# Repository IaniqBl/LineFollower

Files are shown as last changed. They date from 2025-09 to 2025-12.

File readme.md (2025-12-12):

# LineFollower

Mijn LineFollower  
afbeelding

## specifications

microcontroller: Arduino Nano

motors: N20 1/50 500RPM

h-bridge: DRV8833

sensors: QTR-8A

batteries: 2S LiPo 1500mAh

wireless communication: HC08

distance sensor - motors: 10,5cm

weight: x

speed: x

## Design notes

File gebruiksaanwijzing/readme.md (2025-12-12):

# Gebruiksaanwijzing

### opladen / vervangen batterijen
Koppel de batterij los van de linefollower.  
Gebruik een balanceerlader om hem via de balansconnector op te laden.  
Koppel los na het opladen en laat de batterij rusten.  
Koppel de batterij terug aan de linefollower.  

### draadloze communicatie
#### verbinding maken
Gebruik de Serial Bluetooth Terminal app.  
Ga naar devices=>Bluetooth BLE=>Scan selecteer het juiste device.  
Keer terug en klik naast het vuilbakje op connect.  

#### commando's
debug [on/off]  : Toon 1 maal de debug waardes  
start : Start de linefollower
stop : Stopt de linefollower  
set cycle [µs] : Stelt de cyclus tijd in
set power [0..255] : Stelt de power in (255 => 8.4V)
set diff [0..1] : Stelt de diff in  
set kp [0..] : Stelt de kp in  
set ki [0..] : Stelt de ki in  
set kd [0..] : Stelt de kd in  
calibrate black : Calibreer de zwarte waardes  
calibrate white : Calibreer de witte waardes  

### kalibratie
Zet de linefollower op de zwarte lijn en gebruik het calibrate black command. Deze maakt meerdere metingen en pakt het gemiddelde hiervan.  
Zet de linefollower op de witte achtergrond en gebruik het calibrate white command.  

### settings
De robot rijdt stabiel met volgende parameters: 
Kp : 9.00  
Ki : 0.00  
Kd : 0.14  
Diff : 0.55  
Power : 120  

### start/stop button
uitleg locatie + werking start/stop button
Knop bevindt zich op de pcb. Dit is een toggle interrupt laag actieve knop.  
Deze zet een flag aan, die in de loop dezelfde variabele run toggelt.

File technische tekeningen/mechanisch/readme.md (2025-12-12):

## Motor Mounts

Dit project verwijst naar [deze motor mount](https://www.printables.com/model/784474-n20-motor-mount), een origineel ontwerp van de auteur.  
Gelicenseerd onder [Creative Commons BY-NC-SA 4.0](https://creativecommons.org/licenses/by-nc-sa/4.0/)

🔒 **Licentievoorwaarden:**
- ✅ Gebruik en aanpassing toegestaan
- ❌ Geen commercieel gebruik
- ✅ Delen toegestaan onder dezelfde licentie
- ❌ Niet delen zonder naamsvermelding

> “Deze motor mount is gemarkeerd als originele creatie door de auteur. Gebruik vereist correcte attributie en mag niet commercieel zijn.”

---

## N20 Dust Cover

Dit project verwijst naar [deze N20 dust cover](https://www.myminifactory.com/object/3d-print-n20-motor-dust-cover-101243), ontworpen om de motor te beschermen tegen stof.  
Model door de originele auteur, gelicenseerd onder [Creative Commons BY-NC-SA 4.0](https://creativecommons.org/licenses/by-nc-sa/4.0/)

🔒 **Licentievoorwaarden:**
- ✅ Gebruik en aanpassing toegestaan
- ❌ Geen commercieel gebruik
- ✅ Delen toegestaan onder dezelfde licentie
- ❌ Niet delen zonder naamsvermelding

> “Deze dust cover is gemarkeerd als originele creatie door de auteur. Gebruik vereist correcte attributie en mag niet commercieel zijn.”

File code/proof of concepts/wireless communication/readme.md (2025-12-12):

# draadloze communicatie proof of concept
minimale hard- en software waarmee aangetoond wordt dat duplex kan gecommuniceerd worden tussen de microcontroller en een [laptop|smartphone], gebruik makend van [Arduino IDE en Serial Bluetooth Terminal]
<br />
### configuratie
Baudrate Bluetooth 19200  
RX pin van HC08 op D8  
TX pin van HC08 op D7  

Baudrate Seriele 115200  

### opmerkingen

### gebruiksaanwijzing
Stuur test via de app of seriele monitor. Deze stuurt TEST terug naar seriele monitor of app, afhankelijk waar je deze command hebt gestuurd.  
De ingebouwde Led word getoggled door test te sturen.

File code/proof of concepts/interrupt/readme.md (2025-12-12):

# start/stop interrupt proof of concept
Stap 1: Maak de schakeling na volgens het schema.  
Stap 2: Verbind Arduino met PC en upload de code.  

Knop indrukken is ingebouwde Led aan, nog eens drukken is uit.
Media (3)

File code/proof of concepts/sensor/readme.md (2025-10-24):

# Sensoren proof of concept

Stap 1: Maak de schakeling na volgens het schema.  
Stap 2: Verbind de USB met de PC en selecteer de juiste COM poort.  
Stap 3: Open de seriële monitor en beweeg de sensor over de test lijn.  
Voor betrouwbare waarden moet je deze sensor op dezelfde hoogte verschuiven.  
Sensor over zwart => hoge waarde  
Sensor over wit => lage waarde   
afbeelding

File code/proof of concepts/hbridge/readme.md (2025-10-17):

# H-Bridge proof of concept

Stap 1: Maak de schakeling na volgens het schema.  
Stap 2: Verbind Arduino met PC en upload de code.  
Stap 3: Batterijen insteken. En de beide motors zouden moeten draaien.  

Hieronder zie je een foto van mijn schakeling, ik heb momenteel de batterij vervangen door een voeding + Buck step-down convertor omdat ik wacht op mijn batterij.



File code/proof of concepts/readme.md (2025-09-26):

# Proof of Concepts

Een proof of concept is een combinatie van minimale hard- en software om eenvoudig aan te tonen dat iets werkt.  
Proof of concepts kunnen enerzijds als eerste poging dienen om een bepaald onderdeel van het project werkend te krijgen. Anderzijds kunnen ze tijdens het debuggen van het finale project dienen als test om eventuele hardware problemen te elimineren bij onduidelijke problemen.
<br />  
<br />
Een proof of concept bestaat uit
* een elektronisch schema (indien van toepassing)
* minimale code om de voorop gestelde zaken te demonstreren
* minimale uitleg / aandachtspunten
<br />
De elektronische schakelingen van de proof of concepts komen bij voorkeur overeen met deze van de uiteindelijke linefollower, zodat de code zonder aanpassingen op het finale project kan draaien.

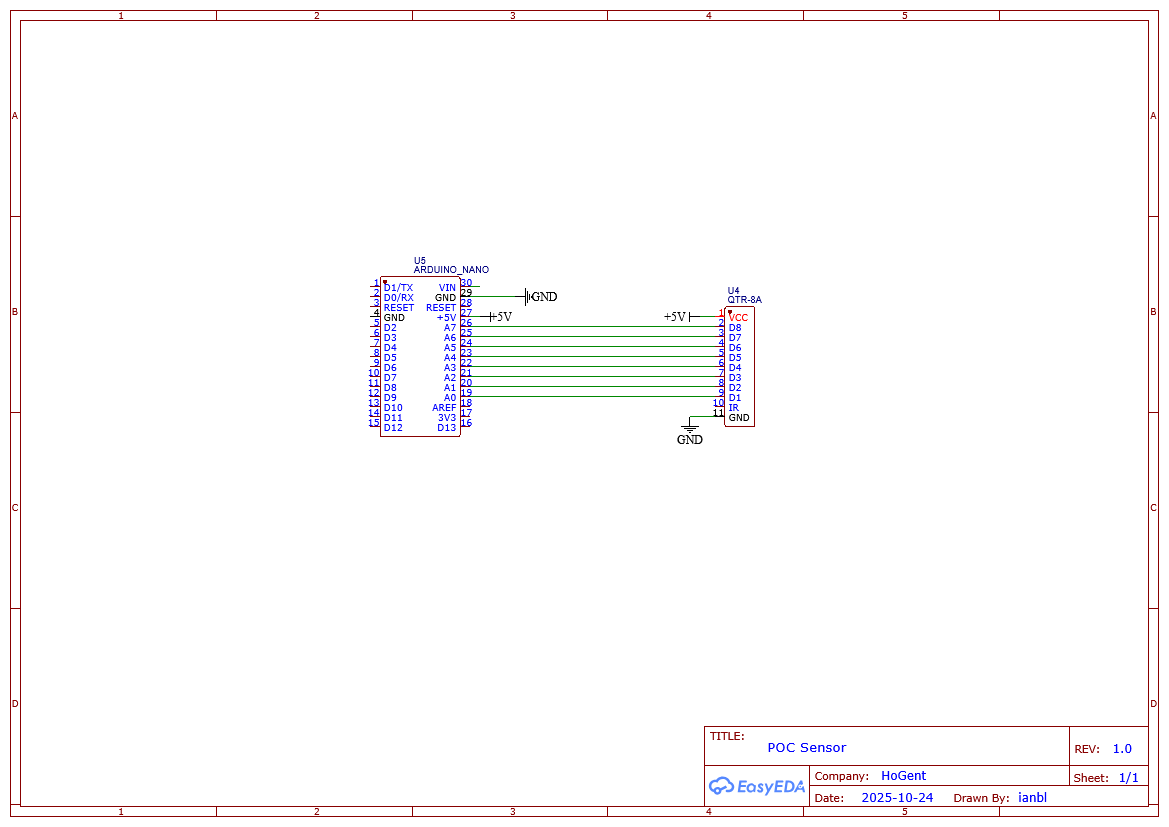
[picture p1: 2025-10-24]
code/proof of concepts/sensor/Schematic_New-Project_2025-10-24.png

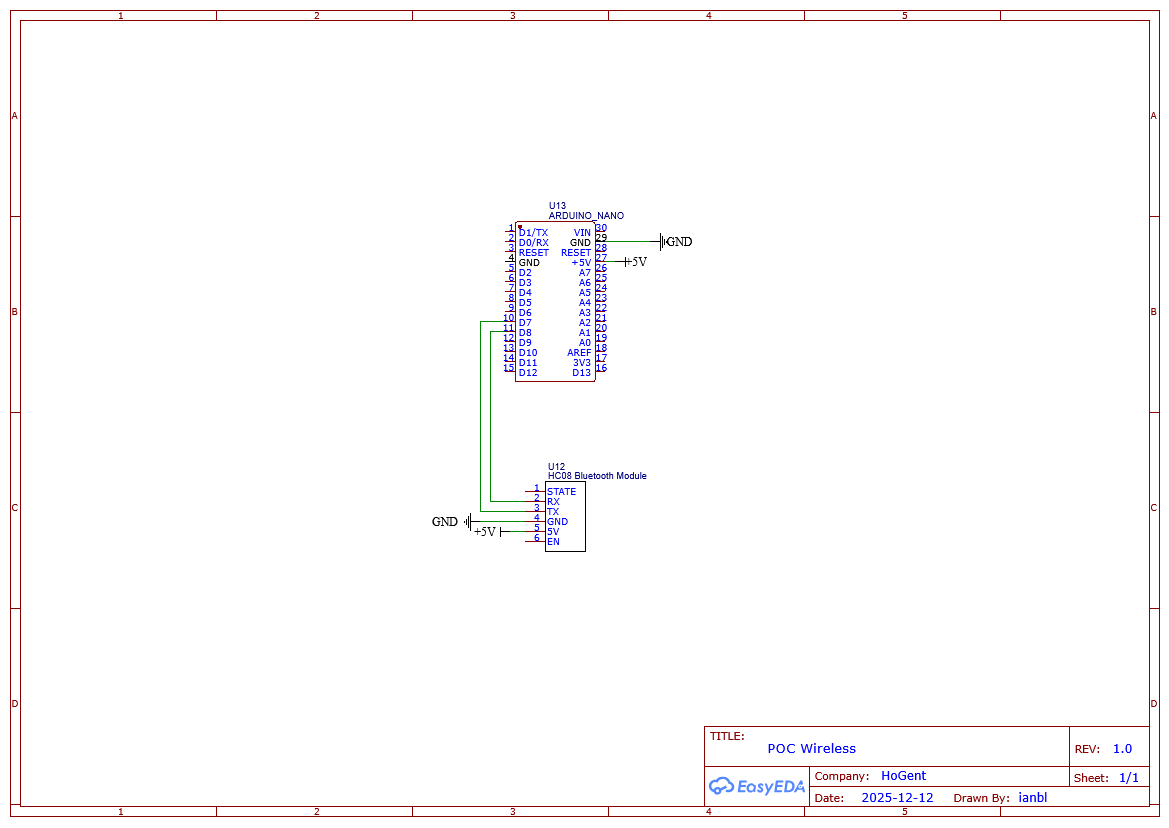
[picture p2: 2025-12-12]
code/proof of concepts/wireless communication/POC_Wireless_Schema.png

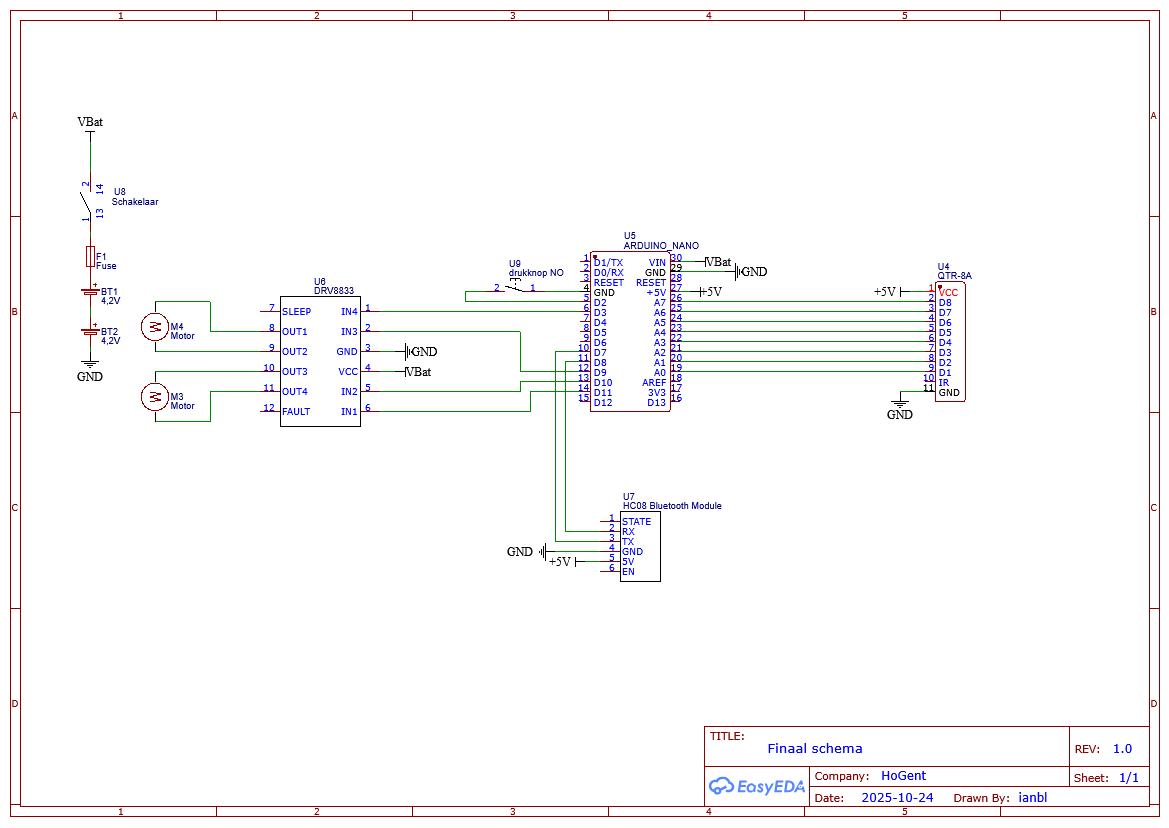
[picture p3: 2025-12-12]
technische tekeningen/elektronisch/Schematic_New-Project_2025-12-12(1).png

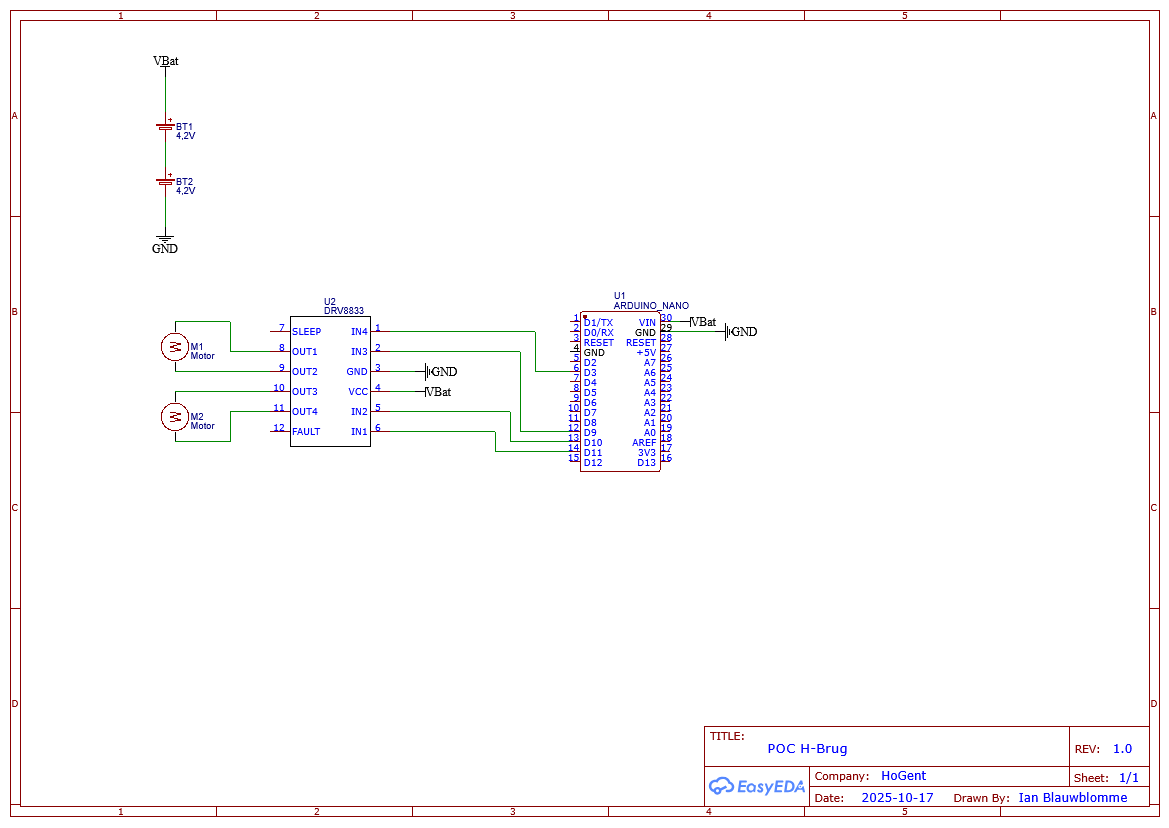
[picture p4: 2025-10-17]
code/proof of concepts/hbridge/POC HBrug Schema.png

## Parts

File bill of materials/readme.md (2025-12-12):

## bill of materials
<br />

|volgnummer|naam|omschrijving|nieuw/recup|kostprijs/stuk|aantal|subtotaal|
|---|----|---|---|---|---|---|
| 1|Arduino Nano|Microcontroller|Nieuw|€ 2,15|1|€ 2,15|
| 2|Knock off QTR-8A|8 Array sensor line follow |Nieuw|€ 2,26|1|€ 2,26|
| 3|N20 6V micro gear 500RPM|Motor|Nieuw|€ 2,16|2|€ 4,32|
| 4|DRV8833|Motor driver|Nieuw|€ 0,61|1|€ 0,61|
| 5|2S Lipo 7,4V 1500 mAh|Batterij|Nieuw|€ 8,45|1|€ 8,45|
| 6|Balans lader|B3EU|Nieuw|€ 6,33|1|€ 6,33|
| 7|Lipo zoemer|Alarm|Nieuw|€ 2,17|1|€ 2,17|
| 8|Wielen|Diameter = 50 mm|Nieuw|€ 1,60|2|€ 3,20|
| 9|XT60 connector|Mannelijke stekker|Nieuw|€ 0,19|1|€ 0,19|
| 10|Schakelaar|Schakelaar batterij|Nieuw|€ 0,55|1|€ 0,55|
| 11|Knop|Start knop|Recup|€ 0,05|1|€ 0,05|
| 12|Pin headers(20)|Female|Recup|€ 0,55|1|€ 0,55|
| 13|Pin headers(20)|male|Recup|€0.55|1|€0,55|
| 14|HC08|Bluetooth module|Recup|€2,43|1|€2,43|
| 15|Smeltzekering|fast blow 3A|Recup|€0,30|1|€0,30|
| 16|Prototype bord|Afmeting: 7x5 cm|Recup|€0,43|1|€0,43|
| 17|Soepele draad|0,5mm²x10m|Nieuw|€2,05 |1|€2,05|
| 18|Soepele draad|0,75mm²x1m|Recup|€0,50 |1|€0,50|
| TOTAAL||||||€37,09|

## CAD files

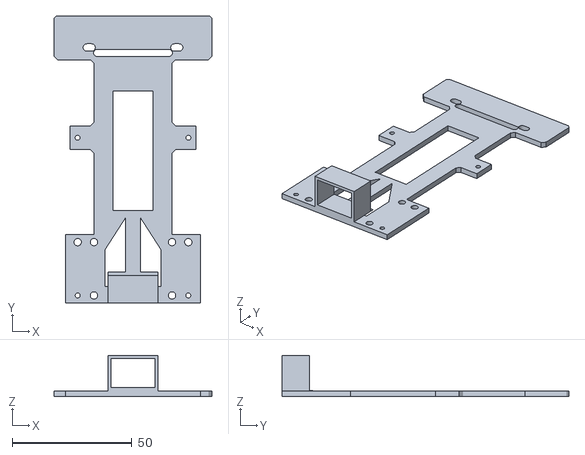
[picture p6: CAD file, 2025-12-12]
technische tekeningen/mechanisch/Chassis.stl
66.0 x 120.0 x 17.2

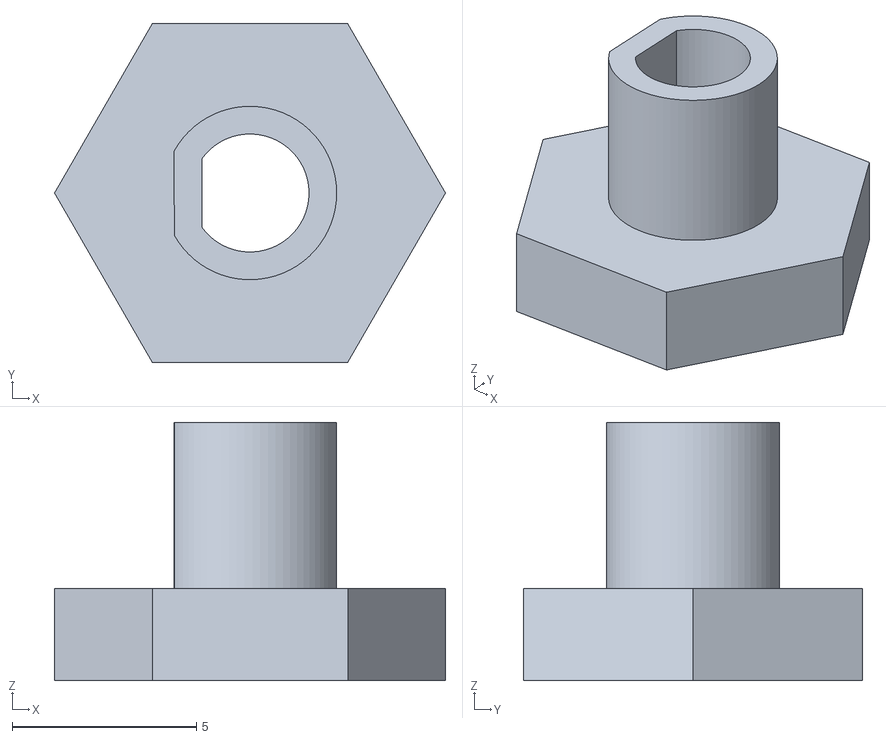
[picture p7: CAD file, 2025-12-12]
technische tekeningen/mechanisch/motor_Das.stl
10.6 x 9.18 x 7.00

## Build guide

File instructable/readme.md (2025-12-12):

# Instructable

Een instructable is een stappenplan - zonder verdere uitleg - hoe je vertrekkend van de bill of materials en gebruik makend van de technische tekeningen de robot kan nabouwen. Ook de nodige stappen om de microcontroller te compileren en te uploaden staan beschreven.  

### stap 1
bestel alle componenten uit de bill of materials  

### stap 2
Test alle componenten aan de hand van de proof of concepts.

### stap 3
Verbind de arduino met de PC. Selecteer de juiste com poort en het juiste bord.
Druk op uploaden. Zorg dat de seriele monitor in arduino IDE op de juiste baudrate staat (115200).  
En dat de seriele monitor op Both NL & CR staat.

### stap 3
Soldeer alle componenten op de printplaat zoals op de elektrische schema's  
Voorzie 10 male headers op de pcb voor het connectoren met de sensor via dupont draadjes.
Voorzie ook de nodige female headers voor de arduino, motor driver, bluetooth module zodat je eenvoudig kan verwisselen indien kapot.  

### stap 4
Test ofdat alles werkt na het solderen, de commands, het eeprom geheugen, de knop.  
Controleer ofdat de motoren in de juiste richting draait, maak gebruik van het test blad

### stap 5
Calibreer de sensor door linefollower op zwarte lijn te plaatsen en via Seriele Bluetooth terminal calibrate black te sturen.  
Plaats hem nu op de witte achtergrond en gebruik calibrate white.

### stap 6
Verbind via arduino IDE en geef het command debug in.  Zet nu de cycle time iets groter dan de calc tijd.  

### stap 7
Gebruik nu de commands voor kp = 1 , diff = 0,1 , ki en kd = 0, power = 100.  
Controleer met debug of er nergen Nan staat.  

### stap 8
Test nu ofdat de motoren in de juiste richting draait door middel van het test blad. 
In het midden => beiden draaien vooruit  
Links => Linkerwiel sneller dan rechter of rechter draait trager/achteruit.  
Rechts => Rechterwiel sneller dan linker of linker draait trager/achteruit.
Afhankerlijk van je diff zal hij trager of achteruit gaan.  

### stap 9
Begin nu met instellen van PID regelaar.  
Speel met Kp, diff en power hiermee zou hij al 3 toeren moeten kunnen rijden.  

### stap 10
Introduceer nu de Kd en/of ki zodat hij soepeler rijd.  
Ki heb ik niet gebruikt.
Nu je power omhoog en blijven tunen todat hij stabiel rijdt.

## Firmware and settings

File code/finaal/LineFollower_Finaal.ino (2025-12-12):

#include "SerialCommand.h"
#include <EEPROM.h>
#include <SoftwareSerial.h>

#define SerialPort Serial
#define Baudrate 115200
#define BTBaudrate 19200

// DRV8833 motor control pins
#define MotorLeftForward 3
#define MotorLeftBackward 9
#define MotorRightForward 10
#define MotorRightBackward 11

#define MAX_PWM 255


bool run;
float iTerm = 0;
float lastErr = 0;

volatile bool buttonPressed = false;
volatile unsigned long lastInterruptTime = 0;

SoftwareSerial BTSerial(7, 8);   // RX, TX

SerialCommand sCmdUSB(SerialPort);
SerialCommand sCmdBT(BTSerial);

unsigned long previous, calculationTime;
const int sensor[] = {A0, A1, A2, A3, A4, A5, A6, A7};

struct param_t {
  unsigned long cycleTime;
  int black[8];
  int white[8];
  int power;
  float kp, ki, kd, diff;
} params;

void onRun();

void onButtonPress() {
  unsigned long now = millis();
  if (now - lastInterruptTime > 150) {   // debounce
    buttonPressed = true;
}
lastInterruptTime = now;
}
void setup() {

  // === ADC prescaler op 32 zetten (ADPS2=1, ADPS1=1, ADPS0=0) ===
  ADCSRA &= ~((1<<ADPS2) | (1<<ADPS1) | (1<<ADPS0));  // eerst wissen
  ADCSRA |=  (1<<ADPS2) | (1<<ADPS1);                  // prescaler = 32
  ADMUX = (1<<REFS0);  // expliciet AVcc + rechts-uitgelijnd

  SerialPort.begin(Baudrate);
  BTSerial.begin(BTBaudrate);

  // motor pins als OUTPUT
  pinMode(MotorLeftForward, OUTPUT);
  pinMode(MotorLeftBackward, OUTPUT);
  pinMode(MotorRightForward, OUTPUT);
  pinMode(MotorRightBackward, OUTPUT);
  pinMode(2, INPUT_PULLUP);
  attachInterrupt(digitalPinToInterrupt(2), onButtonPress, FALLING);


  // USB commando’s
  sCmdUSB.addCommand("set", [](char* cmd){ handleSet(sCmdUSB, SerialPort); });
  sCmdUSB.addCommand("debug", [](char* cmd){ handleDebug(SerialPort); });
  sCmdUSB.addCommand("calibrate", [](char* cmd){ handleCalibrate(sCmdUSB, SerialPort); });
  sCmdUSB.setDefaultHandler([](char* cmd){ onUnknown(SerialPort, cmd); });


  // BT commando’s
  sCmdBT.addCommand("set", [](char* cmd){ handleSet(sCmdBT, BTSerial); });
  sCmdBT.addCommand("run", onRun);
  sCmdBT.addCommand("stop", onStop);
  sCmdBT.addCommand("debug", [](char* cmd){ handleDebug(BTSerial); });
  sCmdBT.addCommand("calibrate", [](char* cmd){ handleCalibrate(sCmdBT, BTSerial); });
  sCmdBT.setDefaultHandler([](char* cmd){ onUnknown(BTSerial, cmd); });

  iTerm = 0;  // Reset I-term bij opstarten
  lastErr = 0;   // Reset D-term

  EEPROM.get(0, params);
  SerialPort.println("EEPROM geladen:");
  handleDebug(BTSerial);  // laat direct alle waarden zien na opstarten

  SerialPort.println("ready");
  BTSerial.println("ready");
}

void loop() {
  if (buttonPressed) {
    buttonPressed = false;
     if (run) {
       onStop();
      } 
      else {
       onRun();
      }
  }

  sCmdUSB.readSerial();
  sCmdBT.readSerial();

  unsigned long current = micros();
  if (current - previous >= params.cycleTime) {
    previous = current;

    int normalised[8];
    for (int i = 0; i < 8; i++)
    {
      long value = readADC(i);
      normalised[i] = map(value, params.black[i], params.white[i], 0, 1000);
    }

    float position = 0;
    int index = 0;

    // Zoek de sensor met de donkerste (laagste) waarde = lijn
    for (int i = 1; i < 8; i++) {
      if (normalised[i] < normalised[index]) index = i;
    }

    if (normalised[index] > 800) { 
      run = false; // stopt direct
      position = 0; //
      } 


    else if (index == 0) {
      position = -52.5;             // 7 × 15mm / 2 = 52.5 mm links
    }
    else if (index == 7) {
      position = +52.5;             // 52.5 mm rechts
    }
    //Kwadratische interpolatie
    else {
      long sZero      = normalised[index];
      long sMinusOne  = normalised[index - 1];
      long sPlusOne   = normalised[index + 1];

      float b = (sPlusOne - sMinusOne) / 2.0;
      float a = sPlusOne - b - sZero;

      // Veiligheid: als a ≈ 0 (bijna rechte lijn overgang) gewoon lineair interpoleren
      if (abs(a) < 3.0) {  // 3 is een veilige grens
        position = index - 3.5;                     // midden van de drie sensoren
      } else {
        position = index - 3.5 + (-b / (2.0 * a));  // klassieke kwadratische formule
      }
      position *= 15.0;  // afstand tussen sensoren in mm
    }
    
    float error = -position; //error = setpoint - input
    float output = error * params.kp;

    if (run) {
      // I-term
      iTerm += params.ki * error;
      iTerm = constrain(iTerm, -510.0, 510.0);  // anti-windup
      output += iTerm;

      // D-term
      float dTerm = params.kd * (error - lastErr);
      output += dTerm;
      lastErr = error;  // update alleen tijdens rijden
    }

    output = constrain(output, -510, 510);

    int powerLeft  = 0;
    int powerRight = 0;

    if (run) {
      // Basis snelheid
      int base   = params.power;
      // Differentieel gedeelte (hoe harder je stuurt, hoe meer verschil links/rechts)
      int diff   = (int)(output * params.diff);      // bijv. output=30 → diff=30*0.8 = 24
      // Stuur-correctie (de echte PID output)
      int steer  = (int)output;

      // Links en rechts berekenen
      powerLeft  = base + diff + steer;
      powerRight = base - diff - steer;

      // Begrenzen op -255..255
      powerLeft  = constrain(powerLeft,  -255, 255);
      powerRight = constrain(powerRight, -255, 255);
    }

    driveMotor(MotorLeftForward,  MotorLeftBackward,  powerLeft);
    driveMotor(MotorRightForward, MotorRightBackward, powerRight);
  }

  unsigned long difference = micros() - current;
  if (difference > calculationTime) calculationTime = difference;
}

void driveMotor(int ain1, int ain2, int power) {

  if (power > 0) {
    // Vooruit
    analogWrite(ain1,  power);
    analogWrite(ain2,  0);
  }
  else if (power < 0) {
    // Achteruit
    analogWrite(ain1,  0);
    analogWrite(ain2, -power);
  }
  else {
    // Stop
    analogWrite(ain1,  0);
    analogWrite(ain2,  0);
  }
}

uint16_t readADC(uint8_t channel) {
  ADMUX = (1<<REFS0) | (channel & 0x0F);  // AVcc + rechts-uitgelijnd
  ADCSRA |= (1 << ADSC);
  while (ADCSRA & (1 << ADSC));
  return ADC;
}


// handlers //
void onUnknown(Stream &port, char *command) {
  port.print("unknown command: \"");
  port.print(command);
  port.println("\"");
}

void onRun() {
  run = true;
  iTerm = 0;  // Reset iTerm
  lastErr = 0;  // Reset D-term
  BTSerial.println("run mode activated");
}

void onStop() {
  run = false;
  iTerm = 0;  // Reset iTerm
  lastErr = 0;  // Reset D-term

  driveMotor(MotorLeftForward,  MotorLeftBackward,  0);
  driveMotor(MotorRightForward, MotorRightBackward, 0);
  
  BTSerial.println("stop mode activated");
  SerialPort.println("stop mode activated");
}

void handleSet(SerialCommand &cmd, Stream &port) {
  char* param = cmd.next();
  char* value = cmd.next();

  if (!param || !value) return;

  if (strcmp(param, "cycle") == 0)
  {
    long newCycleTime = atol(value);
    float ratio = ((float) newCycleTime) / ((float) params.cycleTime);

    params.ki *= ratio;
    params.kd /= ratio;

    params.cycleTime = newCycleTime;
  }
  if (strcmp(param, "ki") == 0)
  {
    float cycleTimeInSec = ((float) params.cycleTime) / 1000000;
    params.ki = atof(value) * cycleTimeInSec;
  }
  if (strcmp(param, "kd") == 0)
  {
    float cycleTimeInSec = ((float) params.cycleTime) / 1000000;
    params.kd = atof(value) / cycleTimeInSec;
  }
  if (strcmp(param, "power") == 0)    params.power = atol(value);
  if (strcmp(param, "diff") == 0)    params.diff = atof(value);
  if (strcmp(param, "kp") == 0)    params.kp = atof(value);

  EEPROM.put(0, params);
  port.println("OK parameter updated");
}

void handleCalibrate(SerialCommand &cmd, Stream &port) {
  char* param = cmd.next();
  if (!param) return;

  if (strcmp(param, "black") == 0 || strcmp(param, "white") == 0) {
    bool isBlack = (strcmp(param, "black") == 0);
    port.print("Kalibreren "); port.println(param);

    // Normale ADC snelheid voor nauwkeurigheid
    ADCSRA = (ADCSRA & ~7) | (1<<ADPS2) | (1<<ADPS1) | (1<<ADPS0); // prescaler 128
    delay(500); // rustig tijd om te plaatsen

    const int samples = 20;
    long sum[8] = {0};
    for (int s = 0; s < samples; s++) {
      for (int i = 0; i < 8; i++) sum[i] += analogRead(sensor[i]);
      delay(5);
    }

    port.print(isBlack ? "black : " : "white : ");
    for (int i = 0; i < 8; i++) {
      int avg = sum[i] / samples;
      if (isBlack) params.black[i] = avg;
      else         params.white[i] = avg;
      port.print(avg);
      if (i < 7) port.print(", ");
    }
    port.println();

    // Terug naar jouw snelle prescaler
    ADCSRA &= ~7;
    ADCSRA |= (1<<ADPS2) | (1<<ADPS1);   // prescaler 32

    EEPROM.put(0, params);
    port.println("klaar + opgeslagen in EEPROM");
  }
}

void handleDebug(Stream &port) {
  port.print("cycle time: "); port.println(params.cycleTime);
  port.print("power: "); port.println(params.power);
  port.print("diff: "); port.println(params.diff);

  float cycleTimeInSec = ((float) params.cycleTime) / 1000000;

  port.print("Kp: "); port.println(params.kp);

  float ki = params.ki / cycleTimeInSec;
  port.print("Ki: "); port.println(ki);

  float kd = params.kd * cycleTimeInSec;
  port.print("Kd: "); port.println(kd);

  port.print("black : ");
  for(int i = 0; i < 8; i++) {
    port.print(params.black[i]);
    if (i < 7) port.print(", ");
  }
  port.println();

  port.print("white : ");
  for(int i = 0; i < 8; i++) {
    port.print(params.white[i]);
    if (i < 7) port.print(", ");
  }
  port.println();

  port.print("calculation time: "); port.println(calculationTime);
  calculationTime = 0;
}

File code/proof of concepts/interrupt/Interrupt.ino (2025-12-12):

volatile unsigned long lastInterruptTime = 0;

void InterruptButton() {
  unsigned long now = millis();

  if (now - lastInterruptTime > 150) {   // debounce
    if (digitalRead(2) == LOW) {        
      digitalWrite(LED_BUILTIN, !digitalRead(LED_BUILTIN));
    }
  }

  lastInterruptTime = now;
}

void setup() {
  pinMode(LED_BUILTIN, OUTPUT);
  pinMode(2, INPUT_PULLUP);
  attachInterrupt(digitalPinToInterrupt(2), InterruptButton, CHANGE);
}

void loop() {
  
}

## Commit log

2025-10-17 Update readme with setup steps for H-Bridge
    Added steps for setting up H-Bridge with Arduino.
2025-10-17 Revise H-Bridge setup instructions and add image
    Updated instructions and added a photo of the circuit.
2025-10-24 Enhance readme with setup instructions for sensors
    Added step-by-step instructions for sensor setup and usage.
2025-10-24 Update readme to clarify power source for sensor
    Removed the note about battery connection since USB can power the sensor.
2025-10-24 Update readme with sensor usage instructions
    Added instructions for sensor readings and image.
2025-10-24 Rename Schematic_New-Project_2025-10-24.png to POC Sensor Schema.png
2025-12-12 Revise instructions for interrupt proof of concept
    Updated the instructions for the interrupt proof of concept.
2025-12-12 Update readme with motor mounts and licensing info
    Added licensing information and details about motor mounts.
2025-12-12 Update motor mount link in readme.md
2025-12-12 Enhance usage instructions in readme.md
    Added detailed instructions for battery charging, wireless communication, and calibration.
2025-12-12 Update distance sensor value in README
2025-12-12 Update instructable with assembly and testing steps
    Added detailed steps for assembling the robot and testing components.
2025-12-12 Enhance command details and calibration parameters
    Updated command descriptions and calibration settings in the readme.
2025-12-12 Update bill of materials with new pricing and details
